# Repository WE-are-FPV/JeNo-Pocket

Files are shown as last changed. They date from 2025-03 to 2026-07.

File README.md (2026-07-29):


> [!NOTE]
> Current version : **1.1.0** (read [changelog](#changelog) for details)

> [!TIP]
> Version **2.0** available on its own page : [JeNo Pocket V2](https://github.com/WE-are-FPV/JeNo-Pocket-V2)

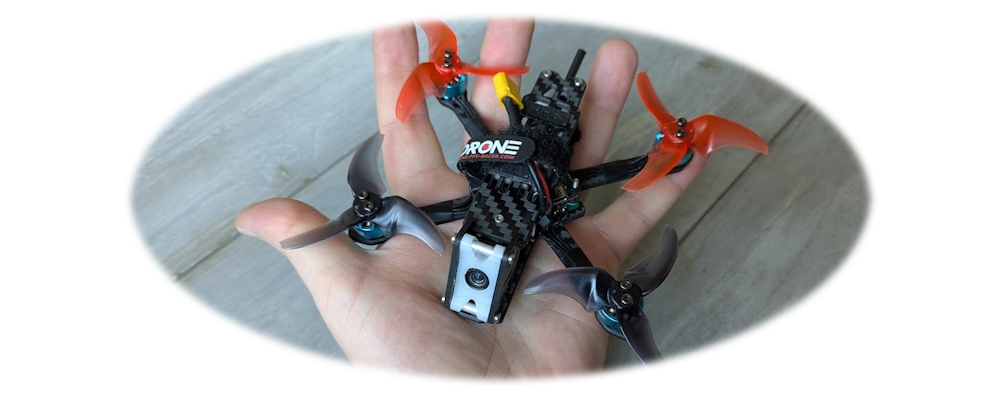
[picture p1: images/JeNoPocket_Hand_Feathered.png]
JeNo Pocket - In the hand


# JeNo Pocket 2.5"
***2.5" drone FPV frame compatible with Air Unit O4 Lite (or any Nano camera), designed for Freestyle, Freeride and Cinematic.***

> [!NOTE]
> Designed in France by members of the [WE are FPV](https://www.wearefpv.fr/) community, the JeNo is already flown by hundreds of pilots and is now being sold by [Drone FPV Racer](https://www.drone-fpv-racer.com/recherche?controller=search&s=JeNo+5.1+frame&aff=64&id_campaign=13) (affiliate link). The French version of the project is available on [Printables](https://www.printables.com/model/1175339-jeno-pocket-drone-frame). Note that a [3-3.5" version](https://github.com/WE-are-FPV/JeNo-3-3.5), a [5.1-6" version](https://github.com/WE-are-FPV/JeNo-5.1) and a [7-8" version](https://github.com/WE-are-FPV/JeNo-7) of the JeNo exist.

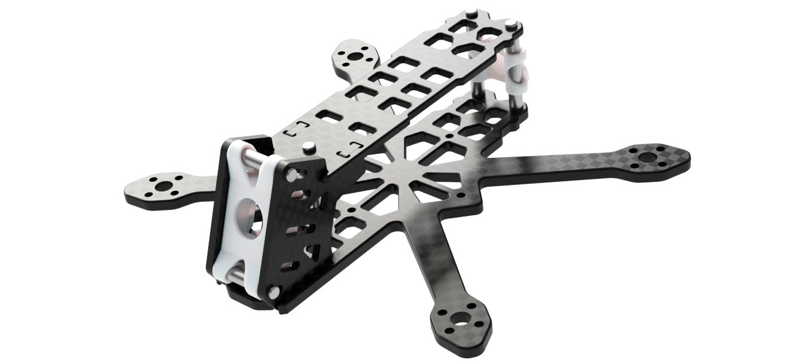
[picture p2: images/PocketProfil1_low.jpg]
JeNo Pocket - 3D render


## Table of contents

* [Key features](#key-features)
* [Presentation](#presentation)
* [Detailed specifications](#detailed-specifications)
* [Alternative Camera Plates (DJI O4 Wide)](#alternative-camera-plates-dji-O4-wide)
* [Bottom Plate Alternative (USB Vertical)](#bottom-plate-alternative-usb-vertical)
* [Recommended configuration](#recommended-configuration)
* [Versions and files](#versions-and-files)
* [Get it cut !](#buy-it-or-cut-it-)
* [Bill of materials](#bill-of-materials)
* [Building/Assembly guide](#buildingassembly-guide)
* [Inspiration](#inspiration)
* [Tuning, Betaflight Preset](#tuning-betaflight-preset)
* [Blackbox](#blackbox)
* [Videos](#videos)
* [Builds examples](#builds-examples)
* [Authors](#authors)
* [TPU](#tpu)
* [Community (remixes and TPU)](#community-remixes-and-tpu)
* [Changelog](#changelog)

## Key features
- [x] Perfect integration of the **DJI Air Unit O4 Lite** camera
- [x] **Wide-X** geometry
- [x] Excellent **flight performance**, easy to tune
- [x] **Sturdiness** and **rigidity**
- [x] Frame, standoffs, and propellers **NOT visible in the video feed**
- [x] **Variable tilt** from 20° to 35°
- [x] Designed for : DJI AU O4 Lite/Wide, WalkSnail, HDZero, Analog
- [x] **Soft-mounted camera** for good stabilization and better durability
- [x] **Roomy** (20 mm high)
- [x] Obviously **Open Source**

## Presentation
**2.5" quads** are **amazing** : playful, lightweight, quiet. You can fly them almost anywhere without risking disturbance or injury. Plus, (almost) everything is cheaper: motors, lipos, props…

The DJI Air Unit O3 and its camera were not suitable for this format, which is why we stopped at the [JeNo 3"](https://github.com/WE-are-FPV/JeNo-3-3.5). But the release of the **Air Unit O4 Lite/Wide** changes everything !

This was the perfect opportunity to give the [JeNo 3"](https://github.com/WE-are-FPV/JeNo-3-3.5) a little brother ! And although there's only a **0.5" difference** in prop size, they are actually very different ! The JeNo Pocket looks **twice as small** and is, in fact, **twice as light** !

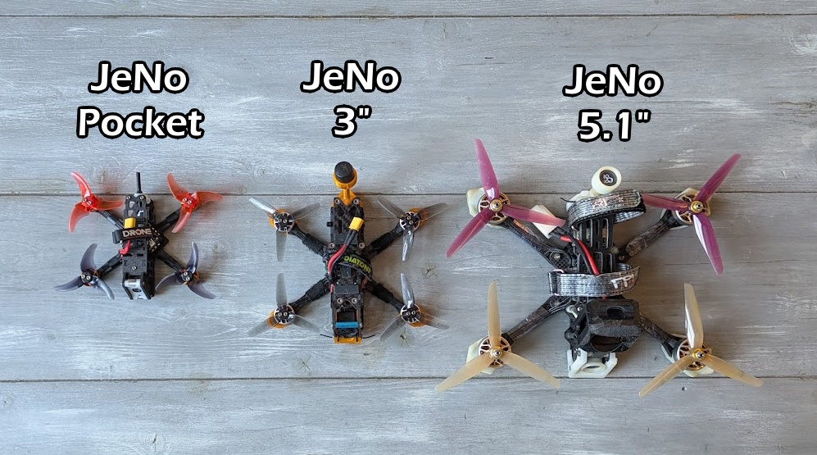
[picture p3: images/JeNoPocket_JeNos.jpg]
JeNo Pocket, JeNo 3" and JeNo 5.1"


Of course, the Pocket retains everything that defines the **JeNo DNA** :

* Carbon camera cage
* High performance and durability
* Spacious and easy to build
* Completely unobstructed video feed (no frame or propellers in view)
* Open Source
* We've also introduced a few extra refinements. For the first time, the **tilt is adjustable** between **20°** and **35°**.

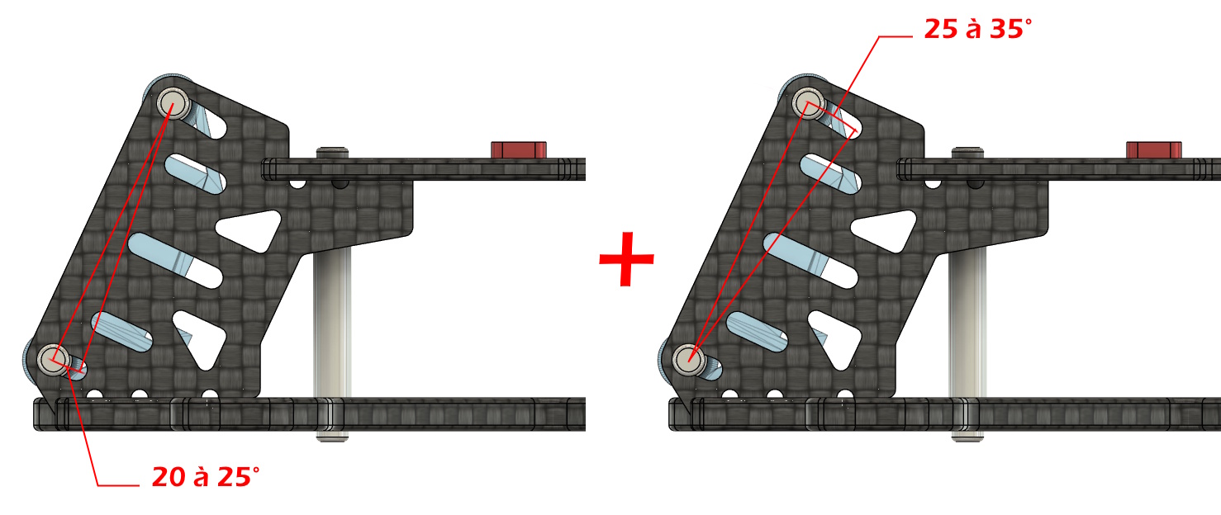
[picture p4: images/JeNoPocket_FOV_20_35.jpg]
JeNo Pocket, Variable tilt


It is possible to use the camera plates to mount the O4 Lite camera using the 16 mm rail spacing, although we do not recommend this approach. Any other **Nano-format** camera should be mountable using the central rail.

The O4 Lite camera is quite sensitive to **vibrations**. For **stabilization** to work properly, it must be correctly **isolated from the frame**. It's not very noticeable, but we’ve maintained a 0.3 mm gap on each side of the mount. The key here is to ensure that the mount is not compressed between the two camera plates.

We’ve included two through-holes to enhance the **soft-mount** effect while also reducing weight. The mount weighs just 1.4 grams. No issues with **Gyroflow** under these conditions!

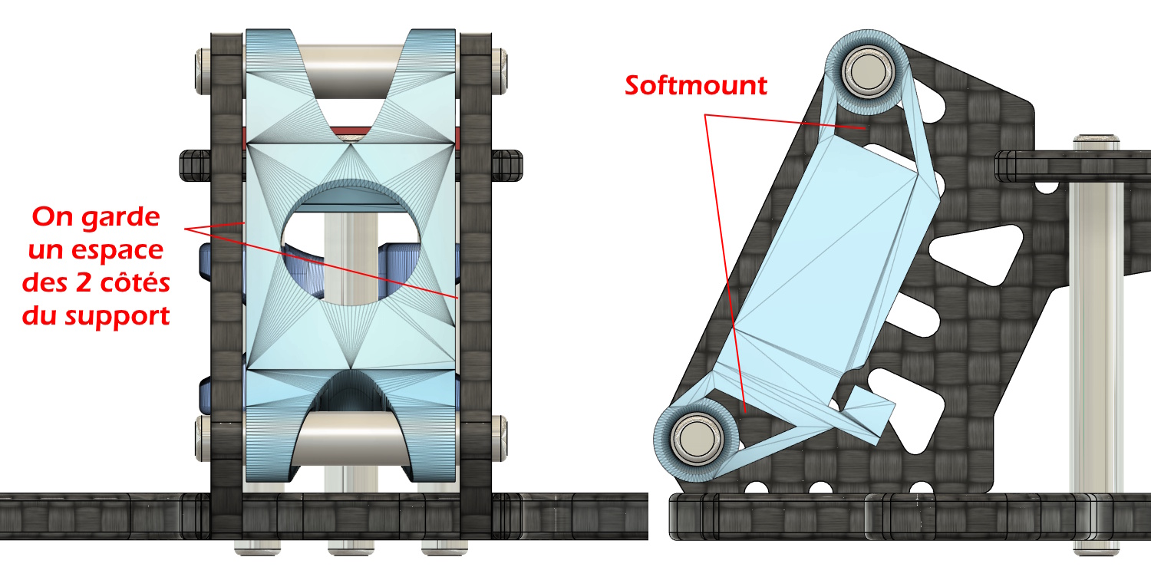
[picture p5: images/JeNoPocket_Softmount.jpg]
JeNo Pocket, Softmount


Although a back stack is no longer needed, we’ve still included a 13 mm x 13 mm area to accommodate an **external RX**, a buzzer, or a capacitor. A small **tab** is also provided to secure a zip tie if needed.

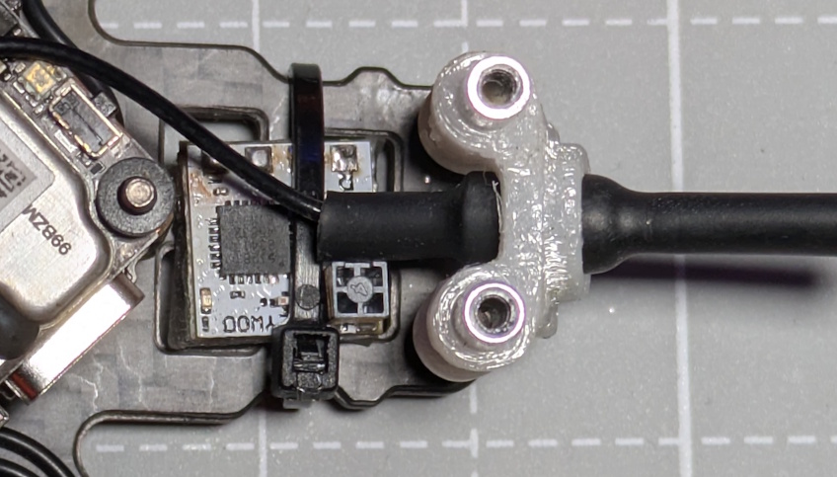
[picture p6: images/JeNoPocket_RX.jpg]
JeNo Pocket, RX Mount


A small capacitor can also be attached to the front standoff (e.g., 220 µF 25V).

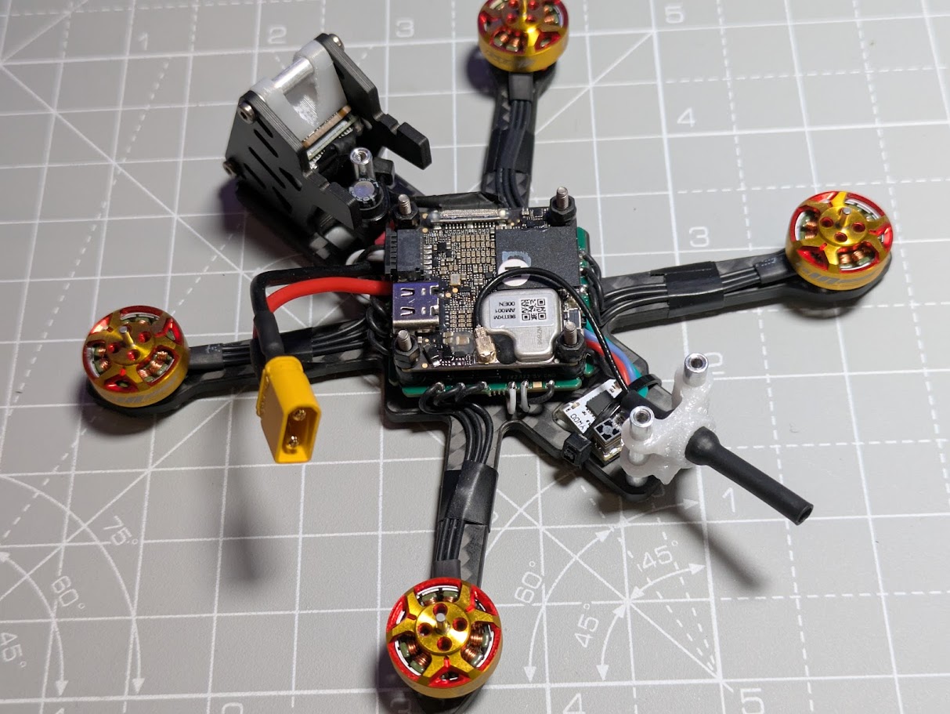
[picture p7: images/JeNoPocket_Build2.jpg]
JeNo Pocket, open build


The JeNo is also available in [3" and 3.5" versions](https://github.com/WE-are-FPV/JeNo-3-3.5), [5.1-6" versions](https://github.com/WE-are-FPV/JeNo-5.1) and [7-8" versions](https://github.com/WE-are-FPV/JeNo-7).

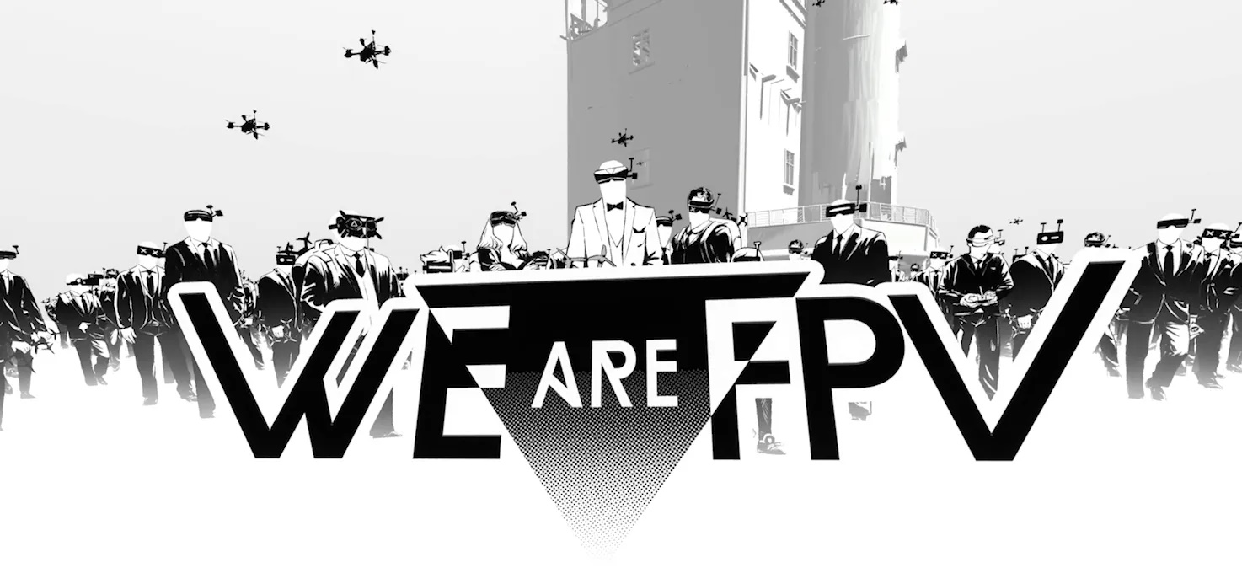
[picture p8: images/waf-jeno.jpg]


## Detailed specifications

|||
| :--- | :--- |
| **Geometry** | **Wide-X** | 
| **Props size** | 2.5" | 
| **Weight** | **24 g**, with screws | 
| **Body height** | 20 mm | 
| **Bottom plate** | 3 mm | 
| **Top plate** | 2 mm | 
| **Camera plates** | 2 mm | 
| **Motors mounting** | 9 mm | 
| **Camera** | 14 mm, Nano, O4 Lite camera. **Clear FOV**. Ajustable. |
| **Main stack** | 30.5 mm x 30.5 | 
| **Back stack** | RX area. 13 mm x 13 mm | 
| **Supported VTX** | Analogic, **DJI Air Unit O4 Lite/Wide**, WalkSnail, HDZero… | 
| **Strap passage** | No | 

## Alternative Camera Plates (DJI O4 Wide)

The **JeNo Pocket V1** was designed partly around the **DJI O4 Lite**. Unfortunately, this model is **no longer available** and has been replaced by the **DJI O4 Wide**. Although the VTX itself is exactly the same, the camera—and particularly its lens and lens mount—is different.

Even though the [JeNo Pocket V2](https://github.com/WE-are-FPV/JeNo-Pocket-V2) has now been released, we wanted to ensure that the JeNo Pocket V1 **remained compatible** with the new **DJI O4 Wide**. We therefore designed **two new sets of camera plates** :

* A **basic** version, with two perfectly identical camera plates.
* A **“reinforced chamfered”** version, featuring additional protection around the lens and a design closer to the original look.

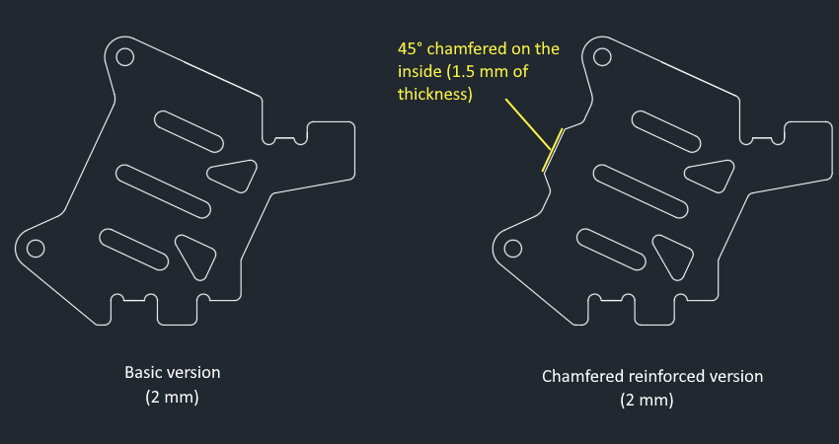
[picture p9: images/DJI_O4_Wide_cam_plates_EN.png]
New O4 Wide camera plates


The **basic version** works perfectly well, is **easier to machine**, and uses the **same plate on both sides**.

The **second version** provides some additional reinforcement around the lens. However, **the chamfer** around the lens protector **is essential**; without it, the camera plates will be visible at the sides of the camera’s field of view. Because of this chamfer, the **left and right camera plates** are **different**.

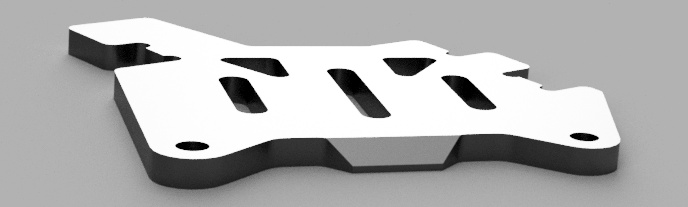
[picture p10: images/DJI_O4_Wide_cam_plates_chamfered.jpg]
Chanfreins


The camera must be moved forward precisely up to the beginning of the chamfer, as shown in the photo below.

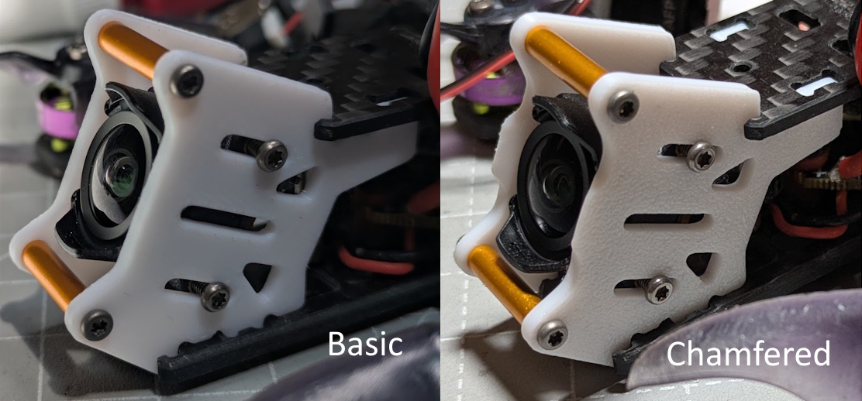
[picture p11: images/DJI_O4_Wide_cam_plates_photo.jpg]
Pictures of the O4 Wide camera plates


This provides the best possible protection.

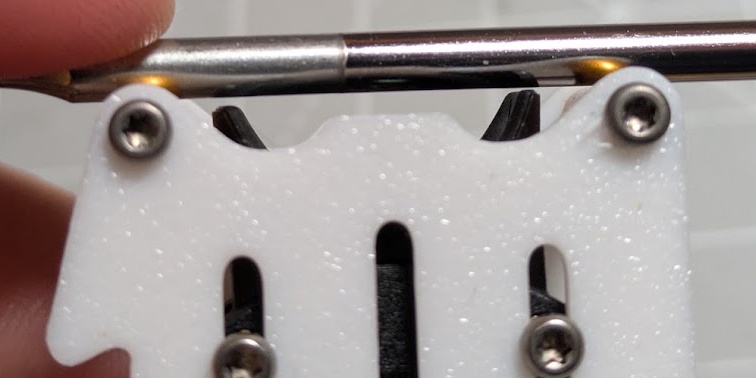
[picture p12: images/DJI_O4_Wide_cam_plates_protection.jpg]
O4 Wide camera protection


## Bottom Plate Alternative (USB Vertical)
Some flight controllers (often for tinywhoops) come with a vertical USB connector. These are **NOT** the FCs we recommend for the JeNo Pocket, as they are often limited to 12A. Instead, we recommend AiOs capable of delivering 20A for peace of mind.

However, with lightweight motor setups, this remains a viable option for the Pocket, **but we strongly encourage you to check your motor power consumption carefully**.

Some pilots were tempted to manually cut a hole to allow for the vertical USB connector. Besides the difficulty of working with carbon fiber and the potential health risks, this modification could weaken the frame and negatively affect flight performance.

For this reason, we have decided to provide an **alternative bottom plate** for the JeNo Pocket, featuring openings at the front and rear to accommodate a vertical USB connector.

If you plan to use such an AiO, you have **two options** :

* Stick with the **standard bottom plate** and place the AiO at the top of the stack rather than underneath. The Pocket’s height allows for this, but to access the connector, you will need to remove the top plate.
* Use the **alternative bottom plate* we have made available.

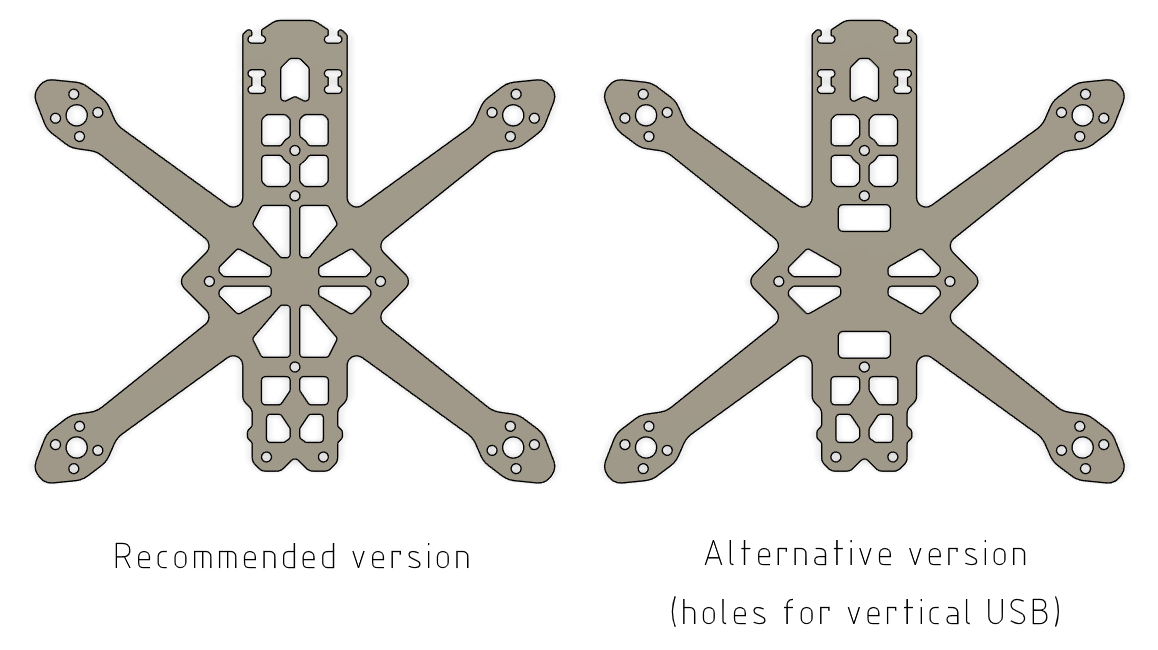
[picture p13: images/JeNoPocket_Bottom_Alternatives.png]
JeNo Pocket, RX options


Warning: The alternative version is currently in beta. It has not been tested yet but should be compatible with AiO FCs featuring a vertical Micro USB or USB-C connector.

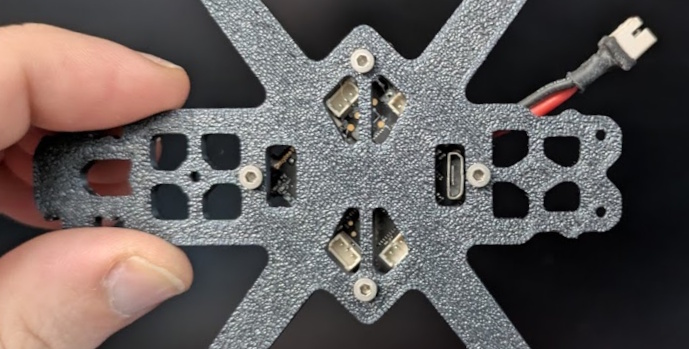
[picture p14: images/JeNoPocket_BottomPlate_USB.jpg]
JeNo Pocket, RX options


## Recommended configuration

Different approaches are possible, from ultra-light to mini-rocket, depending on your hardware choices.

### Motors

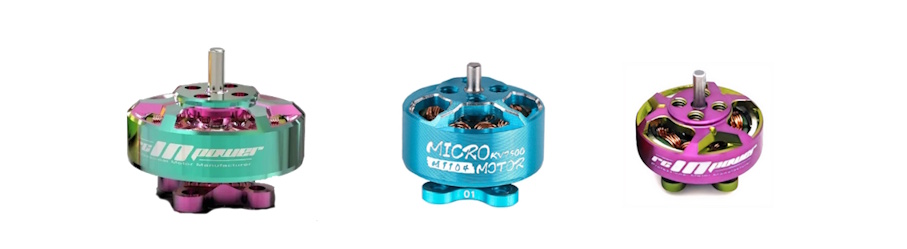
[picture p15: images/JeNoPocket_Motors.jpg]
JeNo Pocket, motors


| **Size** | **Stator volume** | **Recommended KV (2S)** | **Recommended KV (3S)** |
| :---: | :---: | :---: | :---: |
| 1202 | 226 mm³ | ~8000 | ~6000 |
| 1103 | 285 mm³ | ~8000 | ~6000 |
| **1203** | **339 mm³** | **~8000** | **~6000** |
| **1104** | **380 mm³** | **~8000** | **~6000** |
| **1303** | **398 mm³** | **~8000** | **~6000** |
| 1204 | 452 mm³ | ~8000 | ~6000 |
| 1105 | 475 mm³ | ~8000 | ~6000 |

2S motors can also be used on 3S thanks to the **"motor limit"** feature in **Betaflight**.

### Lipos

We recommend **2S or 3S lipos** as indicated in the table above, although 4S is also an option.

**2S ~550 mAh** lipos are a good compromise, or **3S ~450 mAh**. For maximum flight time, **3S ~550 mAh** lipos are still perfectly viable.

Small 2S ~450 mAh lipos are possible with a very light setup and small motors, but the impact on flight time and sag may become noticeable.

In any case, we strongly recommend **Dogcom 2S and 3S 560 mAh** lipos, as they have shown the best performance by far.

<p align="center">
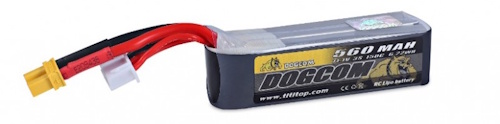
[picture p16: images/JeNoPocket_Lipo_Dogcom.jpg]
  
</p>

Depending on the lipos, during a freestyle flight outdoors in cold weather (~5°C), flight times can range from **2 minutes** (BetaFPV 2S 450 mAh) to **5 minutes** (Dogcom 3S 560 mAh)! You can even hope to reach **7 minutes** with a smooth flight using these same lipos.

### Props
We have always flown the **Avan Rush 2.5"** and are completely satisfied with them.

### FC, ESCs and RX
Here, you’ll have plenty of choices, as the range is very diverse. The main recommendation is to go for an **FC AiO** with ESCs that can deliver **20A**, to be on the safe side, although theoretically, 15A should be sufficient.

The O4 Lite can be powered **directly from the lipo** if you’re using 2S or 3S. For higher voltages, you'll need an FC with a BEC capable of delivering at least 10W for the O4.

Having experienced many unreliable AiOs that didn’t meet the advertised specifications, we recommend opting for **proven hardware**.

Choosing an FC with an **integrated RX** can be a good option to save weight. When they feature a copper antenna, the range is generally quite limited. An **external RX** will often be a better option for range.

Those equipped with a flat antenna or, even better, a ceramic antenna, will offer a good balance of range while minimizing weight gain.

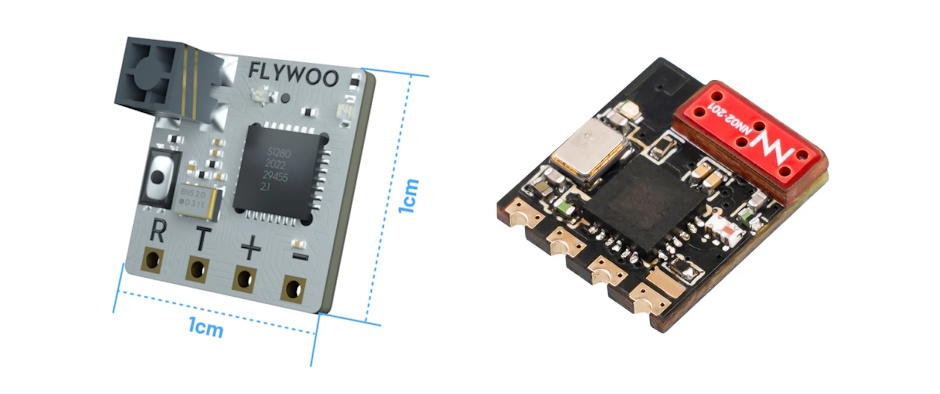
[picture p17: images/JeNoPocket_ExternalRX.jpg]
JeNo Pocket, RX options


The **capacitor** is generally not required for 2S and 3S builds, but if you choose to use one, a **220 µF 25V** will do the job and can be placed either at the front standoff or at the back.

As for the **XT30** pigtail, **18 AWG** cable is a good compromise.

## Versions and files

### Versioning
You will find the **current version** of the frame at the beginning of the description and the full [history of modifications](#changelog) at the end of the page.

We strongly recommend always cutting the latest version to ensure you benefit from the most recent optimizations.

The version **number format** is as follows :
```
<Major versions>.<Minor version>.<Revision>
ex : 1.3.2
```

* **Revision :** This number is incremented in the case of minor modifications with no significant impact.
* **Minor version :** This number is incremented for minor modifications that may potentially break compatibility with certain TPU parts.
* **Major version :** This number is incremented for significant modifications that break compatibility at the carbon level.

Since the creation of the JeNo 5", we have always strived to **maintain compatibility at the carbon level**. As a result, the version remains “1.x.y.”

In practical terms, this means that if you have the very first version of the JeNo 5" and want to equip it with the **O4 Pro**, you only need to have new camera plates cut—they will be compatible with your frame version!

**Note :** If you develop TPU parts for the JeNo, be sure to specify the version they are compatible with.

### Files management
To simplify things, we have reorganized the file structure. The files are now divided into **five groups** :

* **01-FRAME :** Contains **models** describing the **frame** in DXF, STEP, and STL formats for the current version. Also contains a PDF file which is a reformatted version of the DXF.
* **02-TPU :** Contains **TPU models** for the current frame version in STL format.
* **03-FRAME-HISTORY :** Contains previous versions of the frame.
* **04-TPU-HISTORY :** Contains TPU models that are no longer compatible with the current version.
* **OTHER-FILES :** Contains documentation files, including the assembly manual and a description.

The major change is that all options are now consolidated into a single file. This will make version management significantly easier for us.

If you want to view the DXF file with all annotations, we recommend using the free software [DWG TrueView](https://www.autodesk.com/products/dwg-trueview/overview). If you prefer not to use it, the PDF version of the file will contain all the necessary information.

## Get it cut !

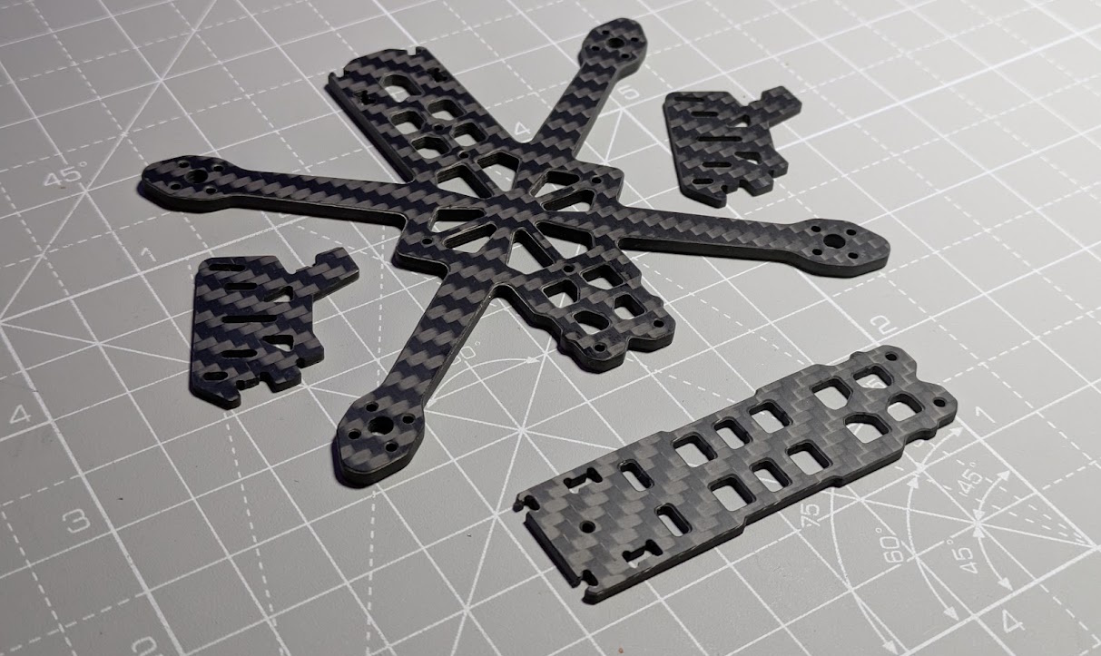
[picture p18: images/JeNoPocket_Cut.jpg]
JeNo Pocket, cut


The JeNo Pocket is available at [FPV CNC Drone](https://fpvcncdrone.com/).

Unlike the 3 and 5" JeNos, the JeNo Pocket won't be available in shops.

The ["01-FRAME"](https://github.com/WE-are-FPV/JeNo-Pocket/tree/main/01-FRAME) folder contains all the files you need to get it **cut**. .DXF and .STEP files are available.

## Bill of materials

In addition to the carbon fiber, you will need the following hardware to complete the assembly of the frame.

**Standoffs**

It is recommended to use 5mm diameter standoffs, especially for those that will serve as support for TPU (backpack and capacitor). Moletted spacers can still be used, but the TPU supports will need to be modified accordingly.

| Quantity | Description | Details |
| :---: | :--- | :--- |
| **3** | **M2x20mm** standoffs **(3.5 or 4 mm diameter)** | for the body |
| **2** | **M2x14mm** standoffs **(3.5 or 4 mm diameter)** | for the camera |

**Stack materials**

20mm screws will comfortably accommodate most configurations. You can use shorter screws if you prefer.
| Quantity | Description | Details |
| :---: | :--- | :--- |
| **4** | **M2x20mm** screws | for the stack |
| **8** | **M2** nylon nuts for the stack screws (4 nuts for the base, 4 nuts on top) | for the stack |

**Frame materials**

| Quantity | Description | Details |
| :---: | :--- | :--- |
| **3** | Minimum **M2x6** mm screws (titanium if possible) | for the top plate |
| **7** | **M2x5-6 mm** screws (titanium if possible) | for the bottom and camera plates |

**Additional materials**

| Quantity | Description | Details |
| :---: | :--- | :--- |
| **12-16** | **M2x5mm** screws if there is NO arm protection between the screw and the motor, otherwise, **M2x6mm**. To save **weight**, you can use only **3 screws per motor**. | for the motors |

## Building/Assembly guide

### Build
The assembly of the frame is straightforward :

<p align="center">
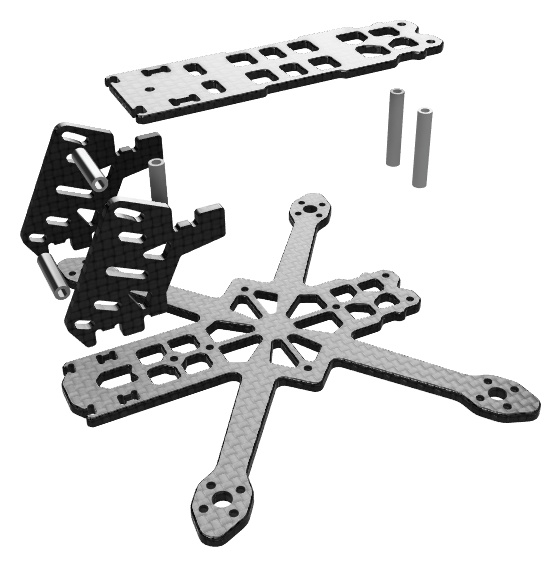
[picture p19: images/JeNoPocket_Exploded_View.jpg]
  
</p>

### Lipo mounting

Two spaces are provided on the top plate to attach two thin strips of **lipo pad** (approximately 16mm x 5mm). It is recommended to use 1.5mm thick lipo pad to minimize weight.

<p align="center">
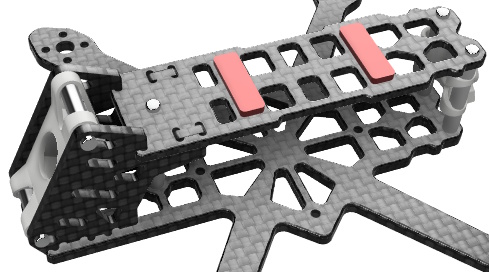
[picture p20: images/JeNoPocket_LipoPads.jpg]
  
</p>

**11-12 cm long straps** will work perfectly for 2S and 3S lipos from 450 to 560 mAh.

We also offer 3 **TPU lipo pads** and 2 custom-cut lipo pads.

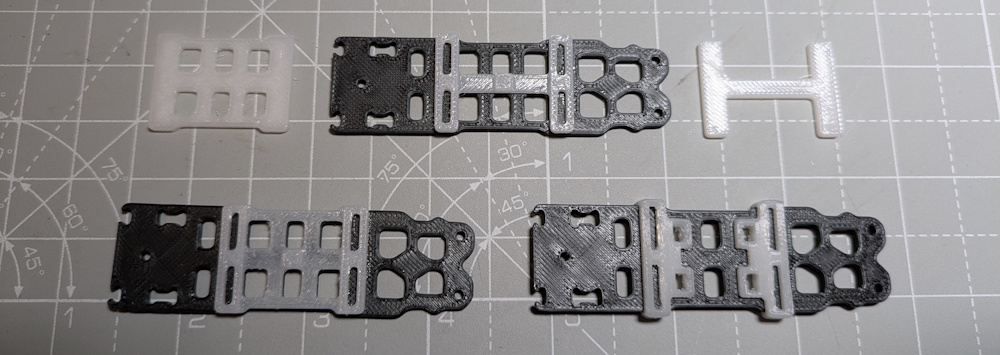
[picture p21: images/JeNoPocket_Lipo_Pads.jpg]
JeNo Pocket, TPU lipo pads


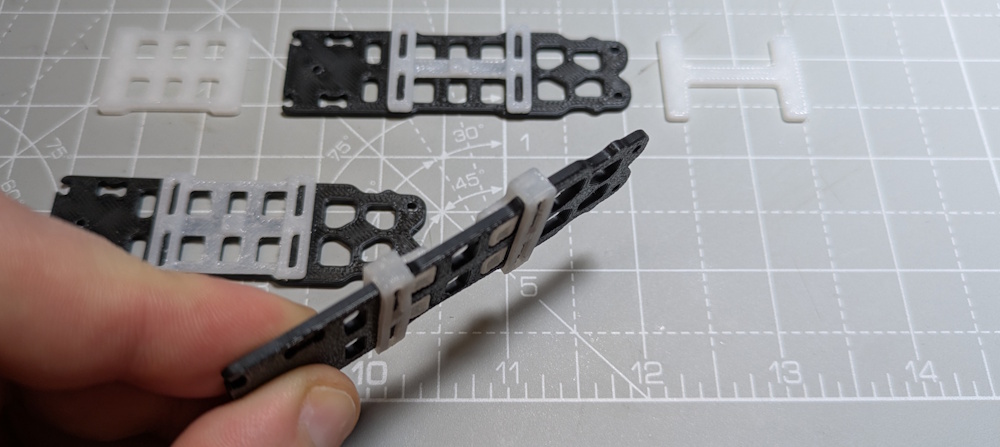
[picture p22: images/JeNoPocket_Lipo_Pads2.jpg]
JeNo Pocket, wrapping TPU lipo pads


* **JeNoPocket_Wrapping_LipoPad.stl** : wraps around and clips into the top plate (0.5g + 0.5g)
* **JeNoPocket_Sticking_LipoPad.stl** : to be glued to the top plate (0.7g)
* **JeNoPocket_Sticking_LipoPad_Light.stl** : to be glued to the top plate, light version (0.5g)
* **JeNoPocket_LipoPad_Cut.dxf** : template for custom lipo pad cutting
* **JeNoPocket_LipoPad_Light_Cut.dxf** : template for custom lipo pad cutting (light)

Since the JeNo Pocket and lipos are so light, using TPU lipo pads is sufficient. They can be paired with an anti-slip strap, but it's not mandatory.

The version that wraps around the top plate is a bit heavier but eliminates the need for glue.

Finally, the openings in the top plate allow you to secure the pigtail with a zip tie in case of lipo ejection.

<p align="center">
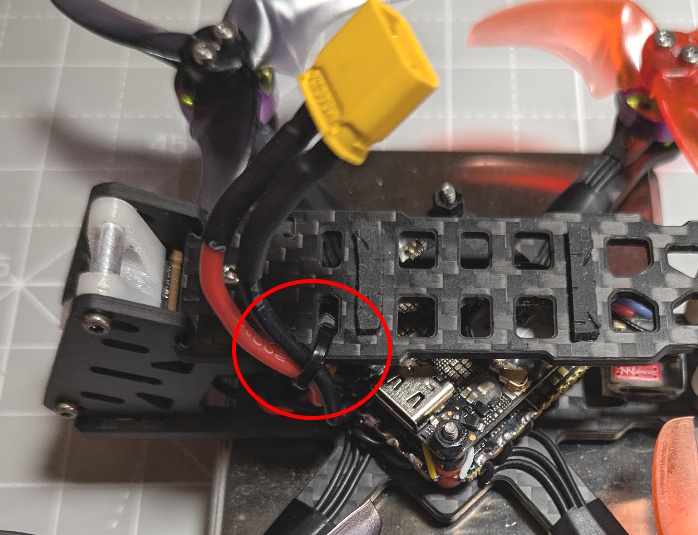
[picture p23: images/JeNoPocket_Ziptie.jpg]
  
</p>

## Inspiration

The **JeNo Pocket** is mainly inspired by its two larger siblings, the JeNo 3 and 5".

**The back stack is no longer needed** with the Air Unit O4 Lite. The front, made up of 2 camera plates, has been designed around the O4 Lite camera.

We kept a 20mm bus height to ensure a **roomy build**, maintain an aesthetic balance with the camera cage, and make sourcing standoffs easier.

## Tuning, Betaflight Preset

**No preset integrated** for now. The behavior of AiOs can vary quite a bit from one to another. We'll wait for more feedback before finalizing anything.

However, here’s an overview of the first tune used for our test flights, which you can use as a starting point if your **Blackbox** is **clean enough**. Note that we’ve activated the profile switch based on the number of cells in the lipo.

As always, be very **cautious** when applying these settings.

**PID profile for 2S :**

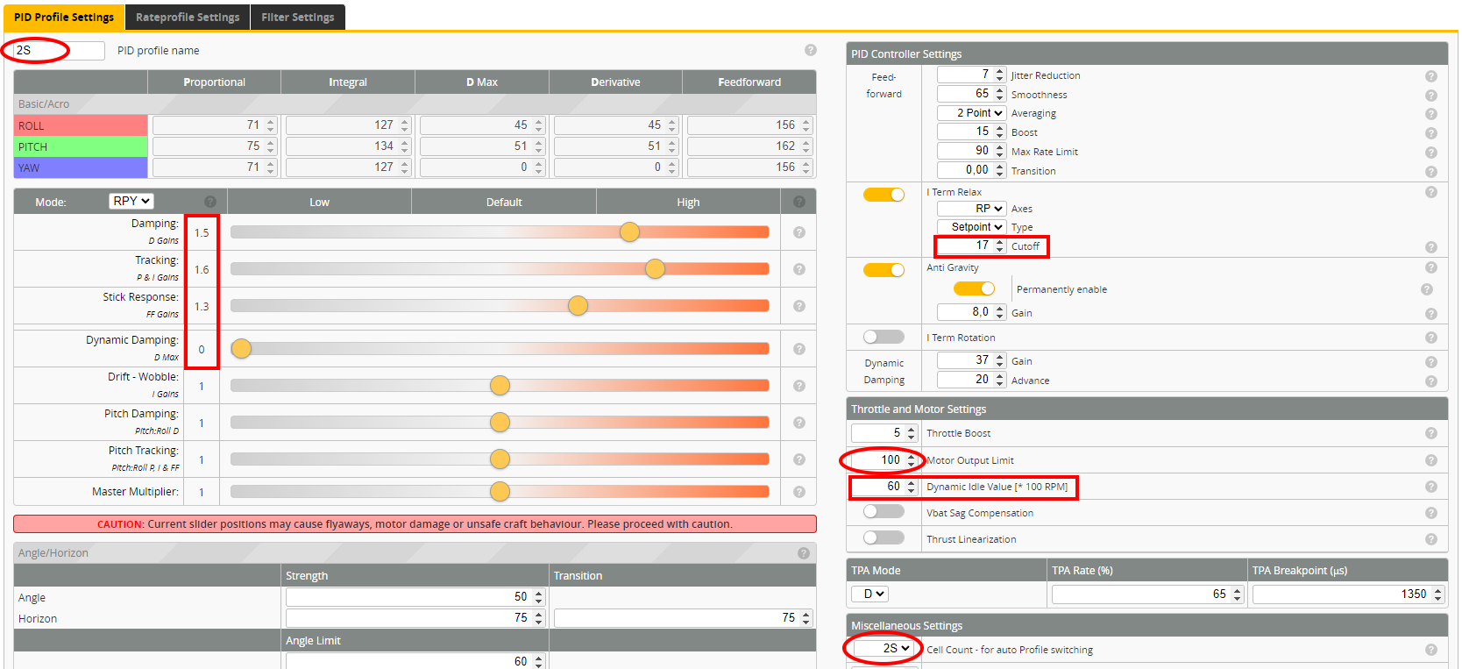
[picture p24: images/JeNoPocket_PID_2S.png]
JeNo Pocket - 2S PID Profile


**PID profile for 3S (8000KV motors limited to 75%):**

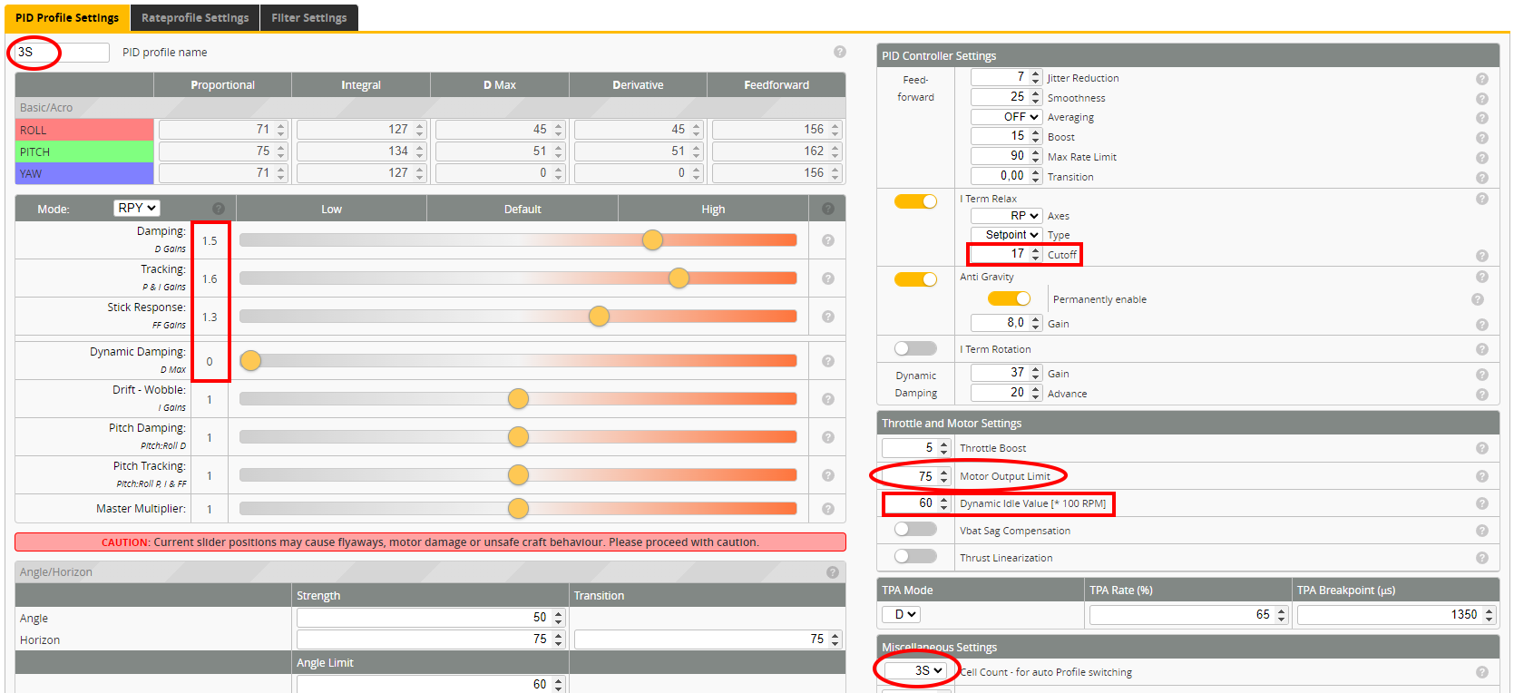
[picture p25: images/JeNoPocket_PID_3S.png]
JeNo Pocket - 2S PID Profile


**Filters :**

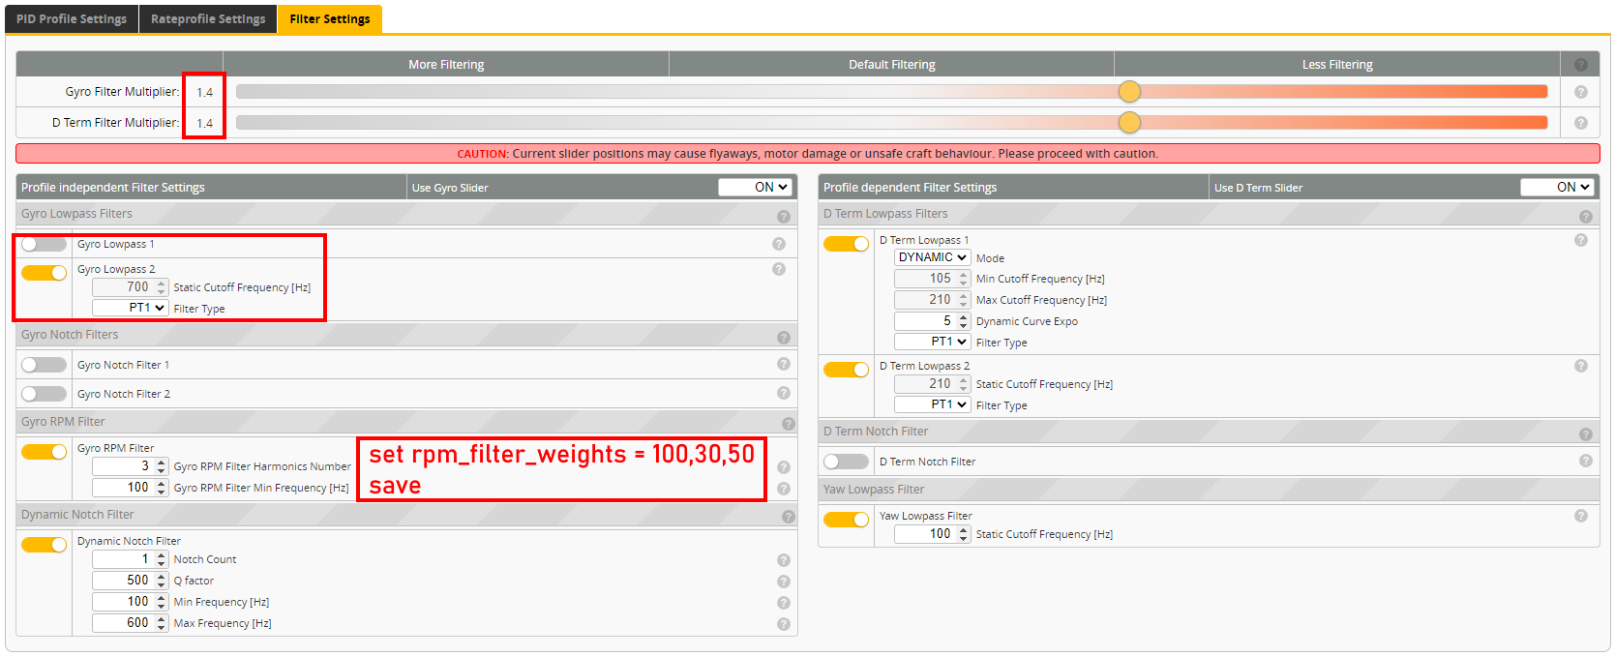
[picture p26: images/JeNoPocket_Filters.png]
JeNo Pocket - 2S PID Profile


## Blackbox

Here’s an overview of the vibration distribution across the 3 axes for the JeNo Pocket. This is the **unfiltered** gyro signal from a tuning flight lasting over a minute:

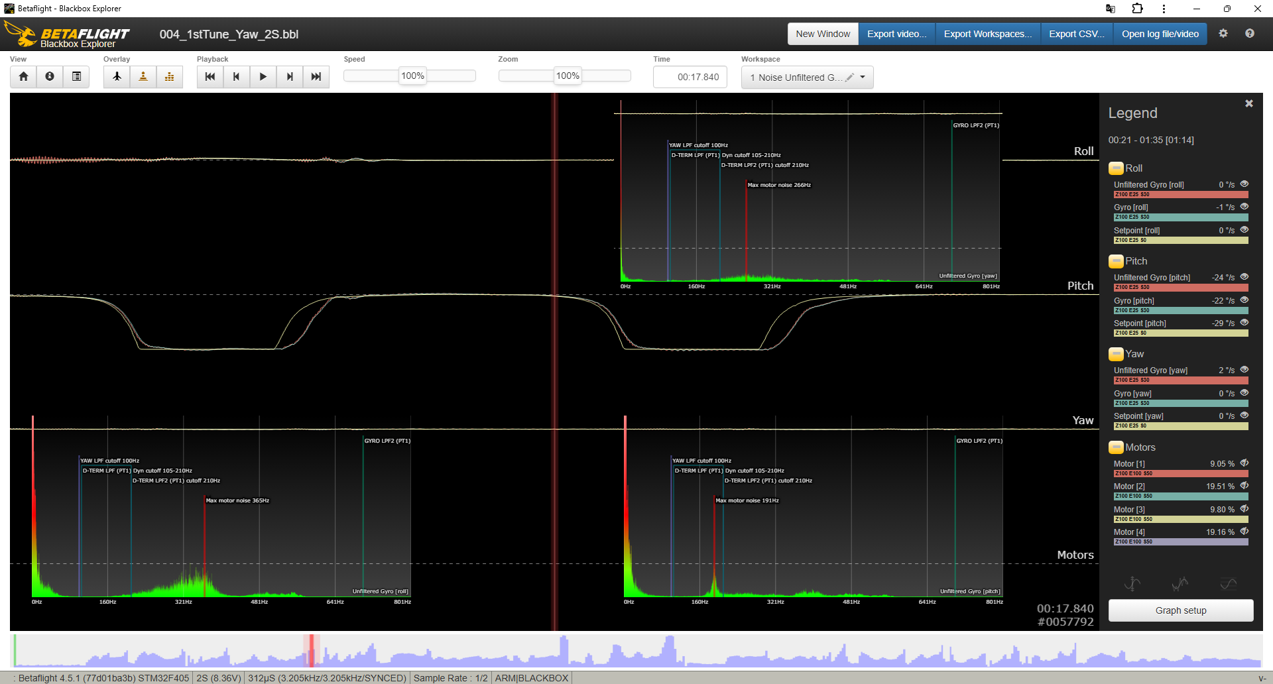
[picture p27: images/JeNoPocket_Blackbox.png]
JeNo Pocket Blackbox


No major spikes, and the signals are easy to filter.

## Videos
Presentation of the **JeNo Pocket** on the **WE are FPV** channel :

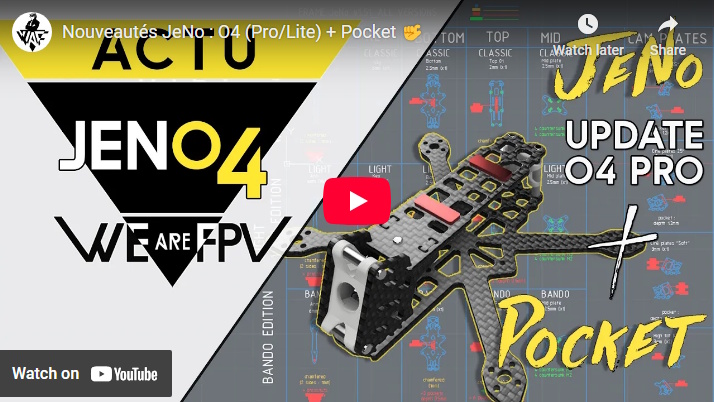
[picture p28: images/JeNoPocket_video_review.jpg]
JeNo 5.1 Maiden (https://www.youtube.com/watch?v=WM7FAgx-Zp0 "JeNo Pocket review on WE are FPV (French) - Click to Watch!")


Demonstration of the **JeNo Pocket's capabilities** (Cinematic, Freestyle Proxy, Freestyle Open Field):

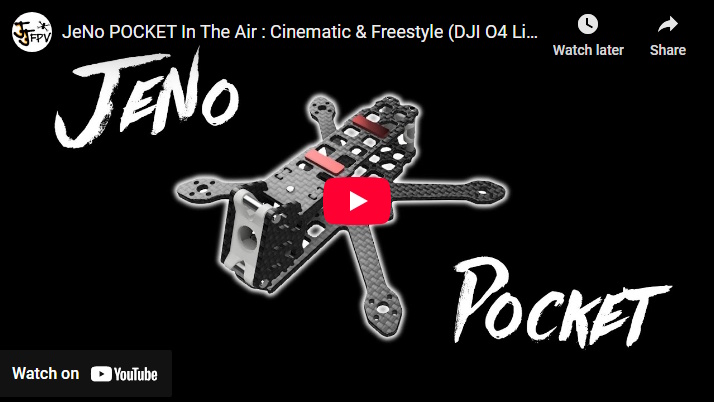
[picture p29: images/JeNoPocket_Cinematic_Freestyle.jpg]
JeNo review on WE are FPV (French) (https://www.youtube.com/watch?v=4OGVIj1YK9c "JeNo Pocket cinematic and freestyle flights - Click to Watch!")


## Builds examples

You can find many build examples on [WE are FPV's DroneBuilds](https://forum.wearefpv.fr/71-dronebuilds/) and [RotorBuilds](https://rotorbuilds.com) :

* fr : [JeNo Pocket 2/3S 1104/1303](https://forum.wearefpv.fr/topic/24092-jeno-pocket) (by Jéjé FPV)
* fr : [JeNo Pocket 2/3S 1203)](https://forum.wearefpv.fr/topic/24204-jeno-pocket-encore/) (by Jéjé FPV)
* fr : [JeNo Pocket Naked Vista/Nebula Pro Nano](https://forum.wearefpv.fr/topic/24201-jeno-pocket-3s-vista-naked-%F0%9F%9A%80/) (by Feisar)
* fr : [JeNo Pocket](https://forum.wearefpv.fr/topic/24178-jeno-pocket-de-nic0/) (by Nic0)
* ...

Find numerous examples of builds on the _**DroneBuilds**_ page of WE are FPV.
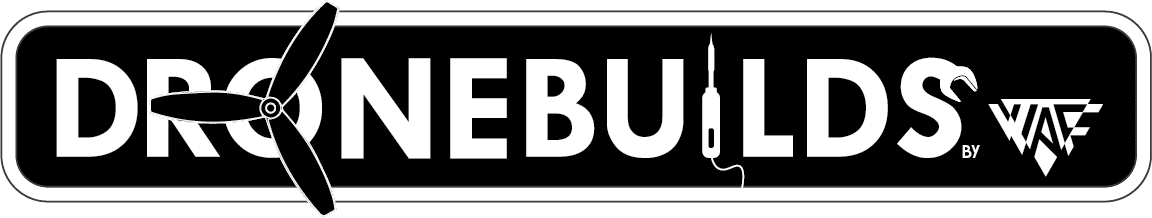
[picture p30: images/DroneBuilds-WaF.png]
DroneBuilds (https://forum.wearefpv.fr/71-dronebuilds/ "DroneBuilds - Click to Access!")


## Authors

The JeNo Pocket was designed by :

* Jerome / Jéjé FPV - [Youtube](https://www.youtube.com/@jejefpv)

## TPU

Among the files to download, you’ll find some TPU parts for your JeNo Pocket. Initially, these include only the camera/antenna mounts for 3.5 or 4 mm standoffs, as well as a few lipo pads.

## Community (remixes and TPU)

**Fork/remix**

If something isn't 100% to your liking on the JeNo Pocket, feel free to check out the community remixes—you might just find what you're looking for:

* [JeNo Pocket Custom](https://www.printables.com/model/1222804-jeno-pocket-custom) by NOX: Modified cutout patterns in the top and bottom plates, plus a slot for a lipo strap.
* [JeNo 25 (Pocket Custom)](https://www.printables.com/model/1236609-jeno-25-pocket-custom) by Cam.Traveler (Marc): Supports 19mm or 14mm cameras, low-profile option, variations from light to bando, and soft-mounted camera plates—all well-documented!
* [O3 Lens mod](https://www.youtube.com/watch?v=PAJpX8I_TqM) by Bard : get great FOV with the DJI O4 Lite

**TPU**

* [Backpack pour ViFly Finder](https://www.printables.com/model/1262438-back-pack-finder-mini-pour-jeno-pocket-25) (by [Tooma](https://www.printables.com/@tomtom_fpv_2283950))

## Changelog

> [!TIP]
> Compatibility is consistently maintained between each version: if your frame was a v1, the parts from v1.2 will be compatible. The same applies to TPU accessories. That's why we don't keep the history of previous versions.

* Version **1.1.0** (17/07/2026)
  * Added two alternative camera plates compatible with the DJI O4 Wide.
* 18/03/2025 :
  * Addition of a unique DXF for all parts + PDF in accordance with other JeNo
* 16/03/2025 :
  * Addition of an alternative bottom plate (untested) for AiO FCs with a vertical USB connector.
* 09/03/2025 : 
  * Added lipo pads (in TPU, to be glued/inserted or custom-cut).
* 17/02/2025 : 
  * Added a few arm protections to screw or clip on, with or without pads.
* Version **1.0.0** (01/02/2025) :
  * Release of the JeNo Pocket in beta version.

## Join the JeNo family !

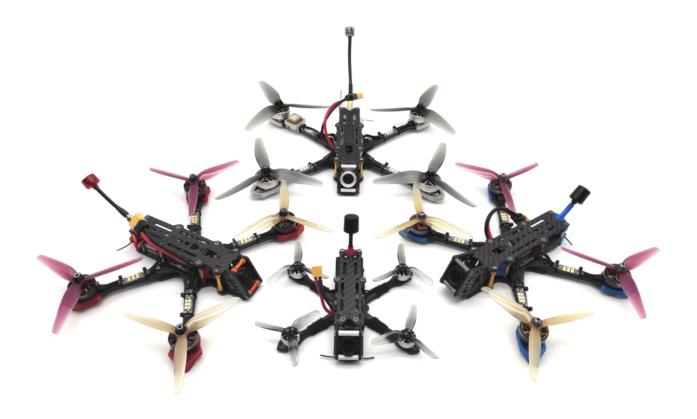
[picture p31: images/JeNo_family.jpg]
||
|:---:|
| JeNo Classic Modus (left), JeNo Cine (right), JeNo 6" (top), JeNo 3" (bottom) |

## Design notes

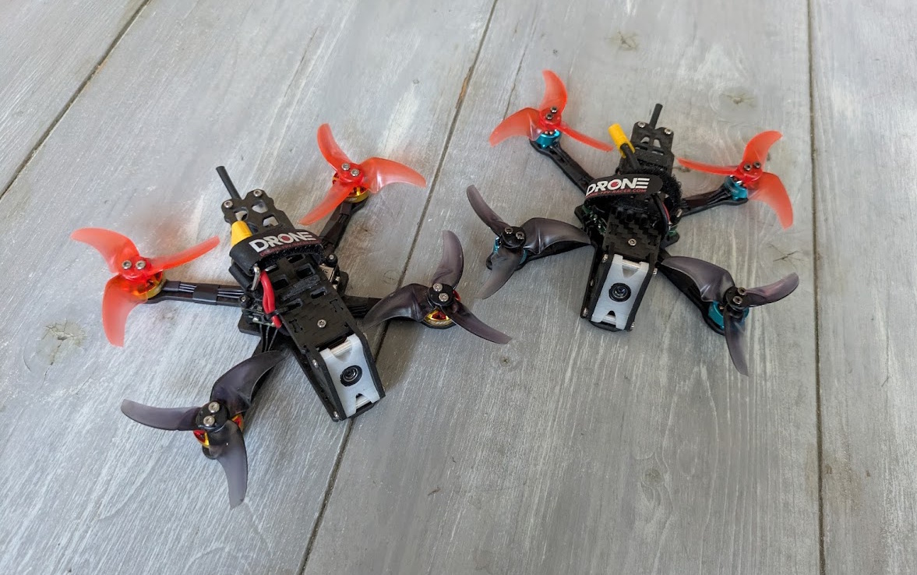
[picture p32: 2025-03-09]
images/JeNoPocket_Bros.jpg

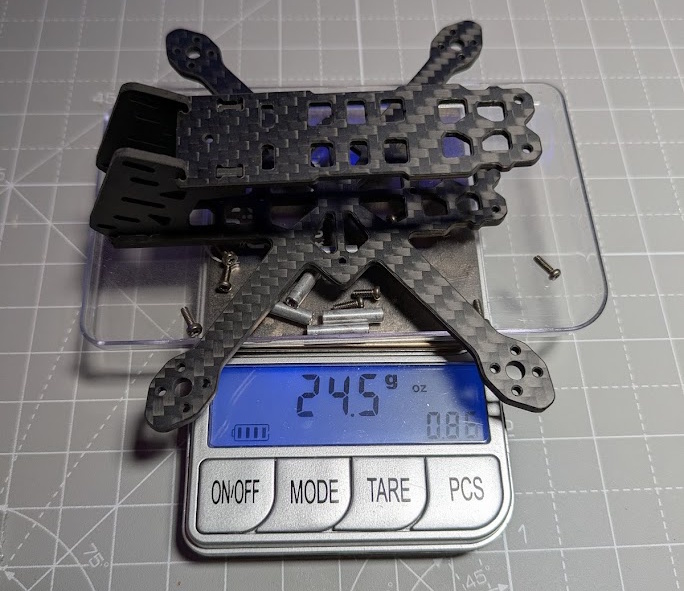
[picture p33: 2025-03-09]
images/JeNoPocket_Frame_Weight.jpg

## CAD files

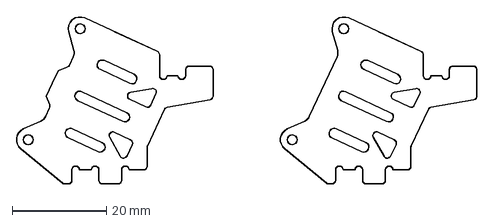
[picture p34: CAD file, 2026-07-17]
01-FRAME/JeNoPocket_1.1_CameraPlates_DJI_O4_Wide.dxf
97.8 x 35.6 mm

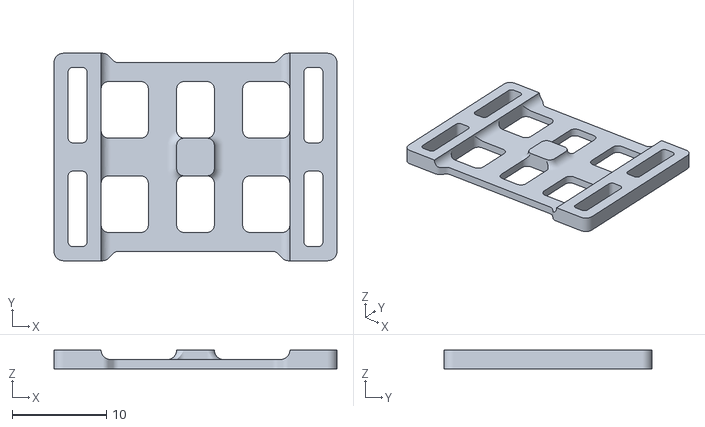
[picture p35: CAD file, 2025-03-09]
02-TPU/JeNoPocket_Sticking_LipoPad.stl
30.0 x 22.0 x 2.00

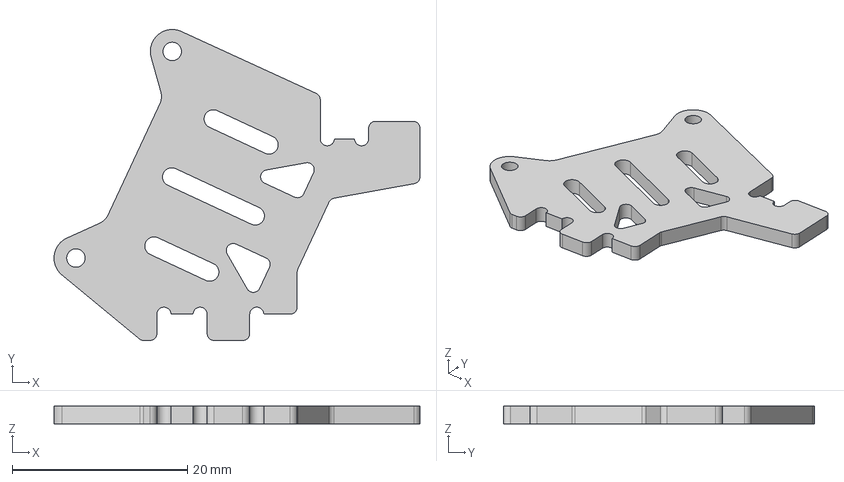
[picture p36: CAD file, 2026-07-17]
01-FRAME/JeNoPocket_1.1_BasicCameraPlate_DJI_O4_Wide.step
41.7 x 35.5 x 2.00 mm

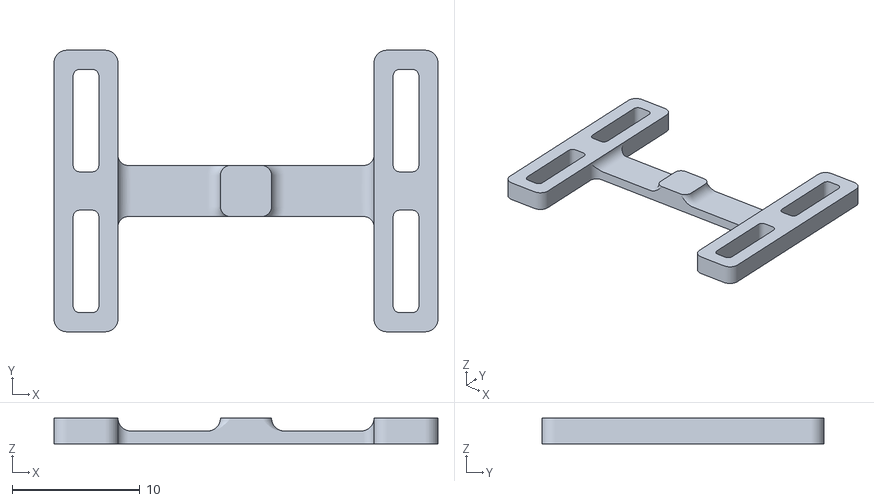
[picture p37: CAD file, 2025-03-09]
02-TPU/JeNoPocket_Sticking_LipoPad_Light.stl
30.0 x 22.0 x 2.00

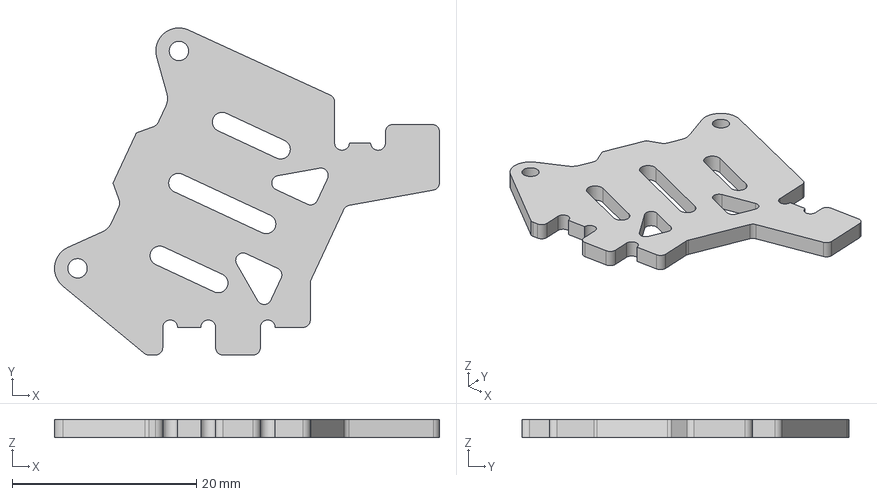
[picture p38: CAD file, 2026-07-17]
01-FRAME/JeNoPocket_1.1_Chamfered_CameraPlate_DJI_O4_Wide_Left.step
41.7 x 35.5 x 2.00 mm

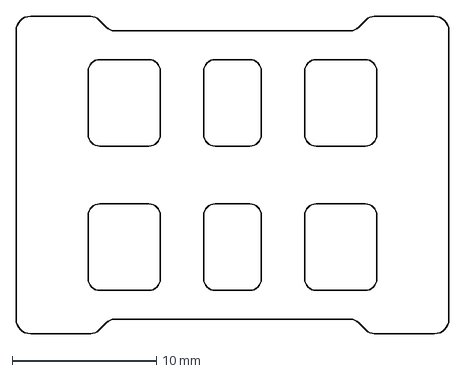
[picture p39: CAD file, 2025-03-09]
02-TPU/JeNoPocket_LipoPad_Cut.dxf
30.0 x 22.0 mm

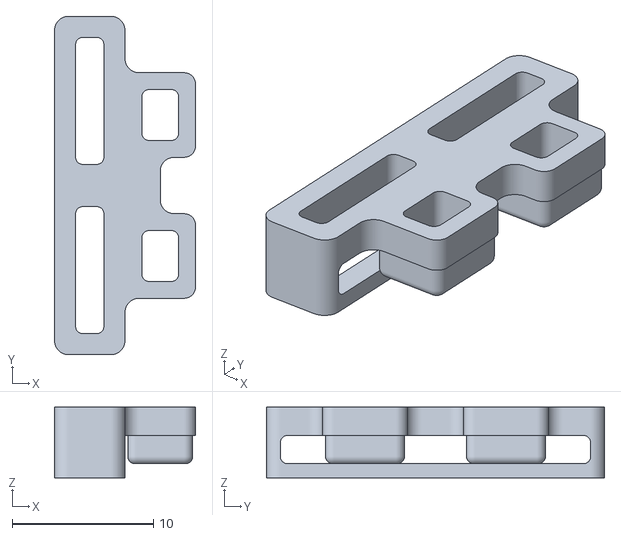
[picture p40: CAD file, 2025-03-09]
02-TPU/JeNoPocket_Wrapping_LipoPad.stl
10.0 x 24.0 x 5.00

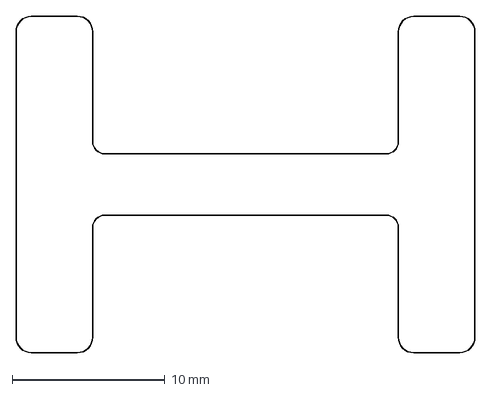
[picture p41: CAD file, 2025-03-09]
02-TPU/JeNoPocket_LipoPad_Light_Cut.dxf
30.0 x 22.0 mm

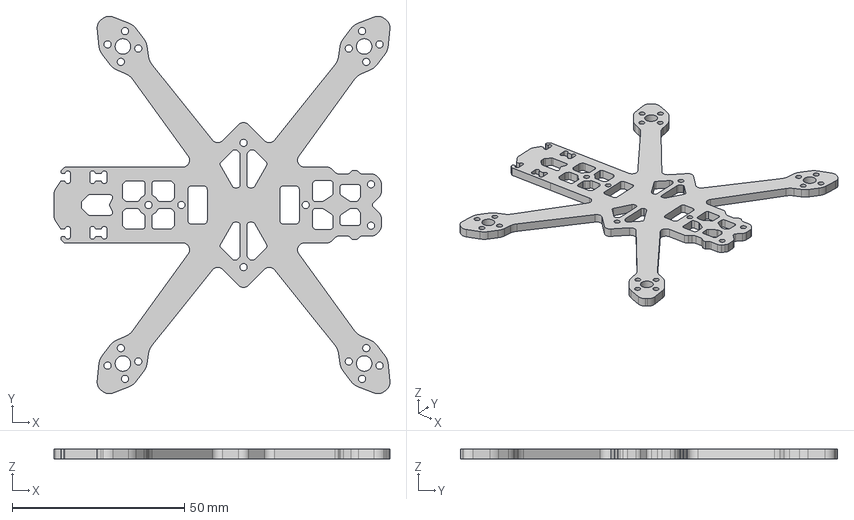
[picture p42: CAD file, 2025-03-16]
01-FRAME/JeNoPocket_1.0_USB_Alternative_BETA.step
97.5 x 109.5 x 3.00 mm

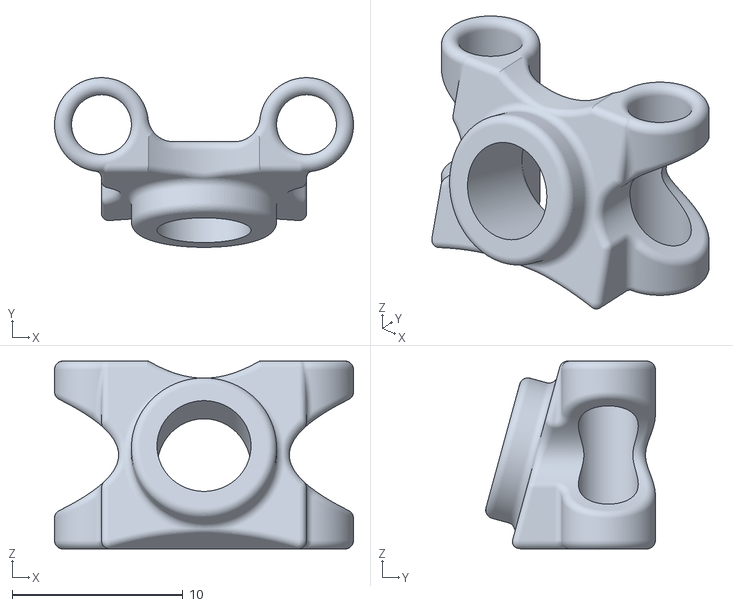
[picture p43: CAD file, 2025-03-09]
02-TPU/JeNoPocket_1.0_VTX_Antenna_3.5mm_Standoffs.stl
17.5 x 9.93 x 11.0

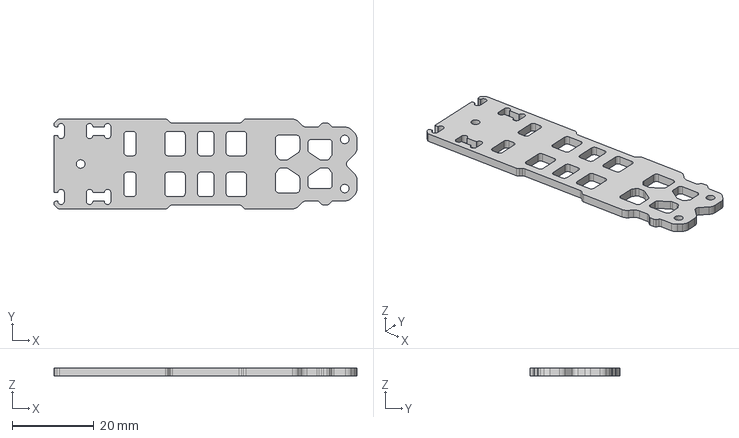
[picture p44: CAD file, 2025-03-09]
01-FRAME/JeNoPocket_1.0_TopPlate.step
74.1 x 22.0 x 2.00 mm

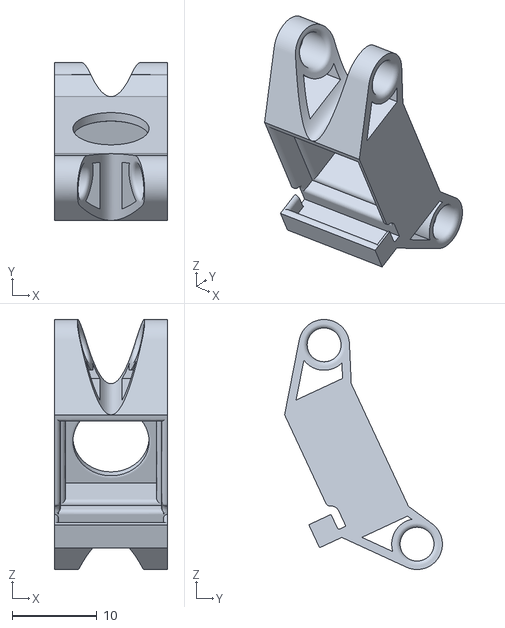
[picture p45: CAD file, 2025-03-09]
02-TPU/JeNoPocket_1.0_O4_Lite_Mount_4mm_Standoffs.stl
13.4 x 18.7 x 29.6

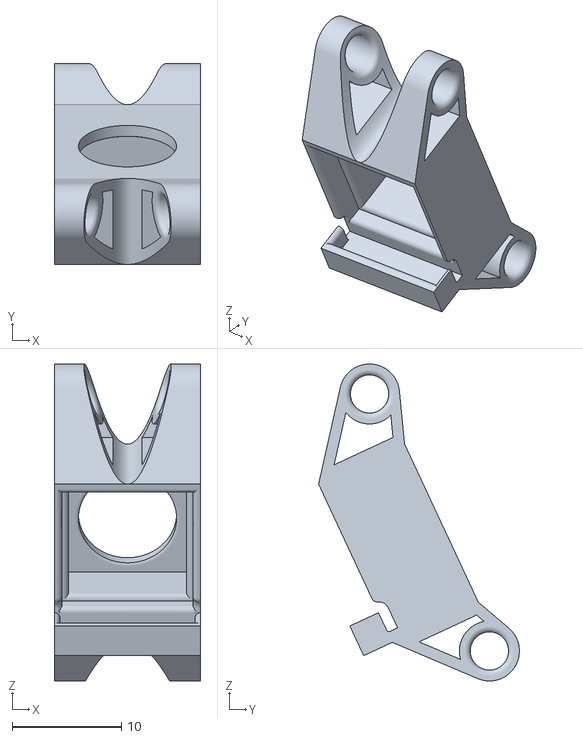
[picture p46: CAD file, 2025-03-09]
02-TPU/JeNoPocket_1.0_O4_Lite_Mount_3.5mm_Standoffs.stl
13.4 x 18.4 x 29.1

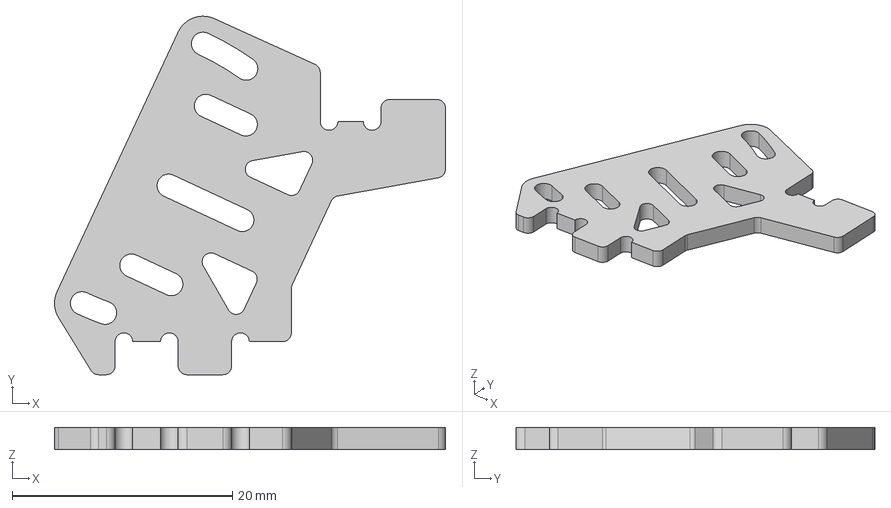
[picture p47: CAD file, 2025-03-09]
01-FRAME/JeNoPocket_1.0_CameraPlate.step
35.5 x 32.6 x 2.00 mm

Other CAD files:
01-FRAME/JeNoPocket_1.1_Chamfered_CameraPlate_DJI_O4_Wide_Right.step
01-FRAME/JeNoPocket_ALL_VERSIONS_1.0.0.dxf
01-FRAME/JeNoPocket_1.0_BottomPlate.step
02-TPU/JeNoPocket_1.0_VTX_Antenna_4mm_Standoffs.stl

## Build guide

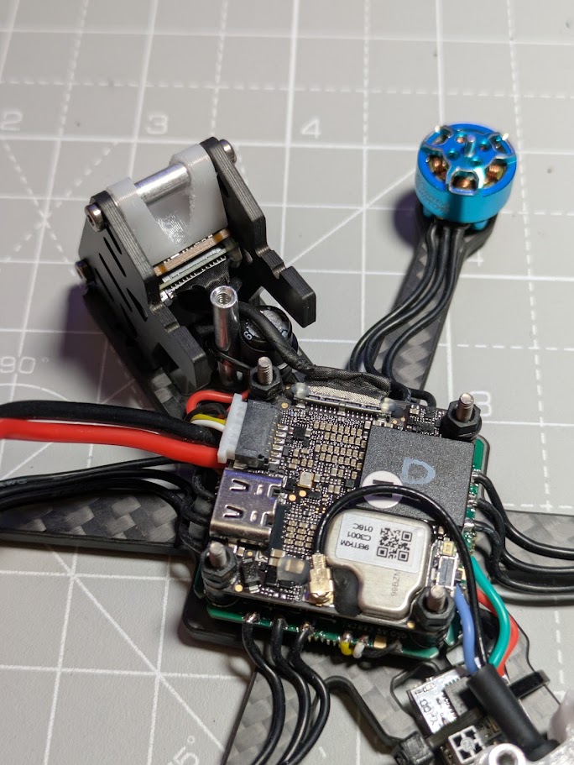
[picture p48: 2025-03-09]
images/JeNoPocket_Build.jpg

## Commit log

2025-03-09 init JeNo Pocket repo
    [JeNoPocket_1.0.dxf, JeNoPocket_1.0_BottomPlate.step, JeNoPocket_1.0_CameraPlate.step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]
2025-03-09 lipo pads
    [JeNoPocket_LipoPad_Cut.dxf, JeNoPocket_LipoPad_Light_Cut.dxf, JeNoPocket_Sticking_LipoPad.stl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]
2025-03-16 add alternative bottom plate for vertical USB connector
    [JeNoPocket_1.0_USB_Alternative_BETA.dxf, JeNoPocket_1.0_USB_Alternative_BETA.step]
2025-03-18 final version of DXF and PDF
    [JeNoPocket_1.0.dxf, JeNoPocket_1.0_USB_Alternative_BETA.dxf, JeNoPocket_ALL_VERSIONS_1.0.0.dxf]

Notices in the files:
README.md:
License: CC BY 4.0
